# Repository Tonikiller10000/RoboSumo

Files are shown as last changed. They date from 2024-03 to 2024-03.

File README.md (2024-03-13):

# RoboSumo

## Description:

This is a SUMO robot for comperitions. It pushes the opponent\`s robot out of the ring.
    
It uses:
- ATmega328p-AU as an microcontroller(used in arduino uno);
- 16 or 20Mhz crystal resonator;
- [TB6612FNG](https://github.com/Tonikiller10000/MotorDriver_1) DC motor driver;
- [VL53L0x](https://github.com/Tonikiller10000/VL53L0x_DistanceSensor) distance sensor;
- LI-PO battery (7.2V)
- 2x DC motors with low torque high speed gear box
- robot suport (Wood, 3d printed or any low weight matherial)

<table>
  <tr>
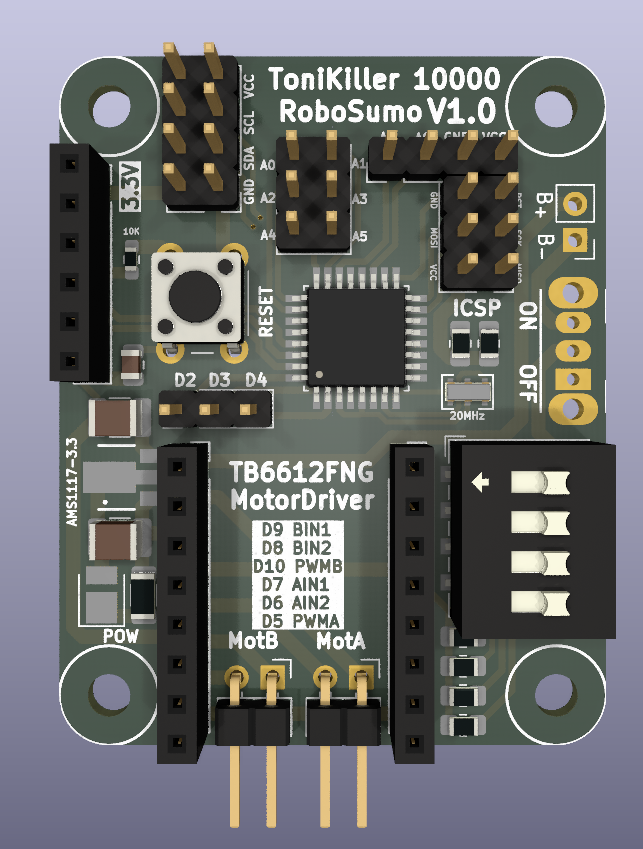
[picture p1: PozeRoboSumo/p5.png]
    <td></td>
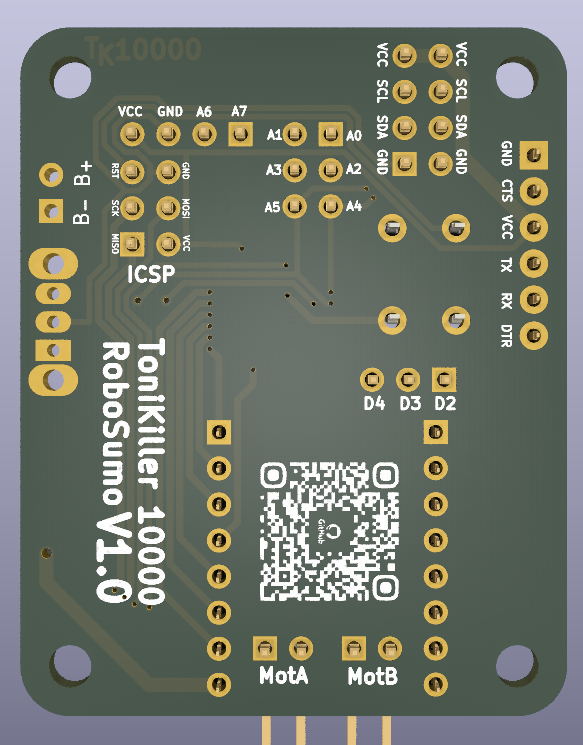
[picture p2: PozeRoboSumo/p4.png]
    <td></td>
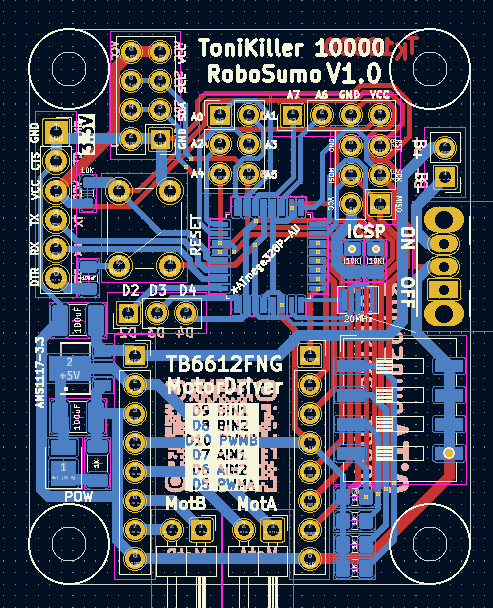
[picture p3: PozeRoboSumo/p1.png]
    <td></td>
  </tr>
</table>

Schematic:
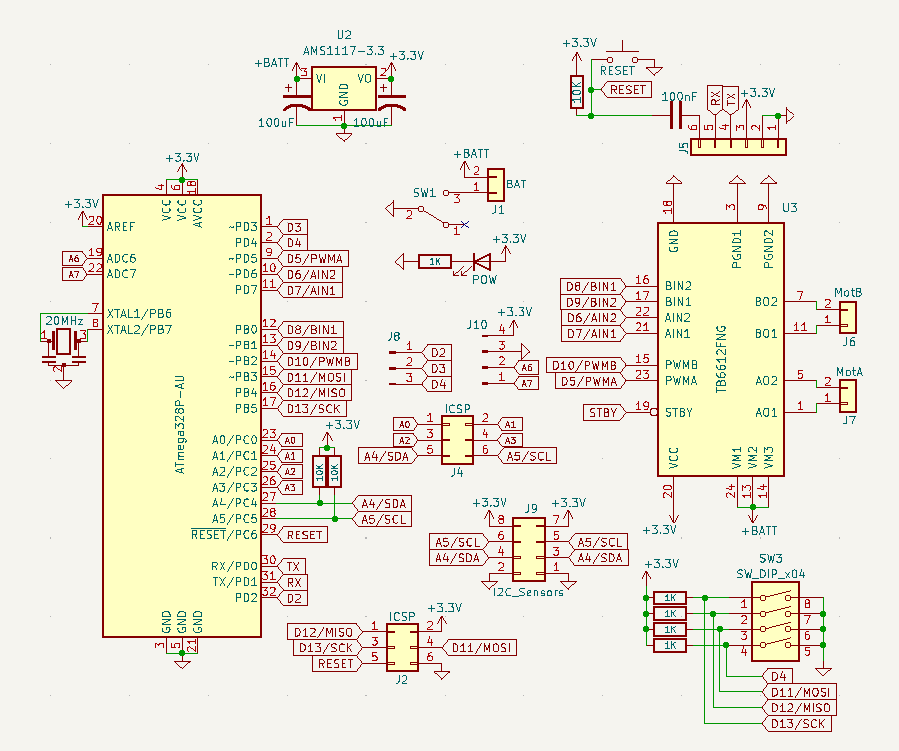
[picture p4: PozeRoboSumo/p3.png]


### How it works:
The board is like a custom arduino UNO board powered from an 7.2V Li-Po battery trouth an 5V voltage regulator. 6 digital pins are used for the TB6612FNG motor driver witch is powered dirrectly from the battery to give more power to the motors. The reset pin has a 10K pullup resistor witch is pulled down by the reset button when it is pressed. The UART and ICSP pins wore pulled out to program the code and the bootloader of the IC.
For now I will try to use the [VL53L0x](https://github.com/Tonikiller10000/VL53L0x_DistanceSensor) I2C distance sensor, because [other sensors](https://github.com/Tonikiller10000/RoboSumo/blob/main/PozeRoboSumo/s1.png) are a little to slow.

### Programming:
Programming of the robot is done via UART protocoll with an [FTDI](https://github.com/Tonikiller10000/CH340G-FTDI-PROGRAMER) programming board. The code for the RoboSumo is not ready. 
 
### Design and mentions

This is The model I followed and some tips:
- to reach better torque on the wheels, it should be wider. 
- to mount the motors use molderd plastic motor holders, or be carefull when printing [it](https://github.com/Tonikiller10000/LineFollower/blob/main/LineFollower_Pictures/w1.jpg). 
- the case was made with autodesk fusion 360 at the 3d printer and with some M3 screws.

<table>
  <tr>
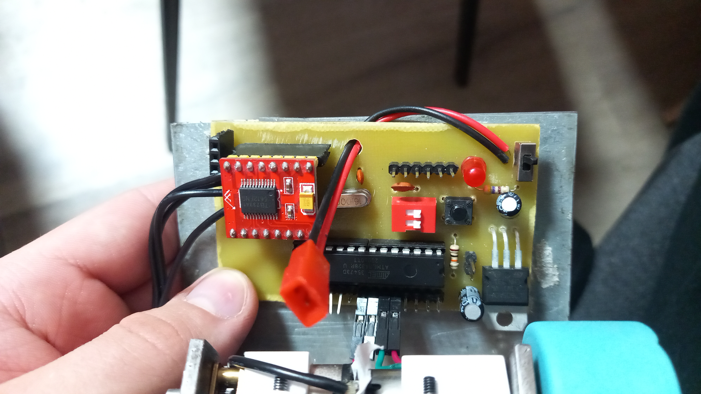
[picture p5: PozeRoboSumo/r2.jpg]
    <td></td>
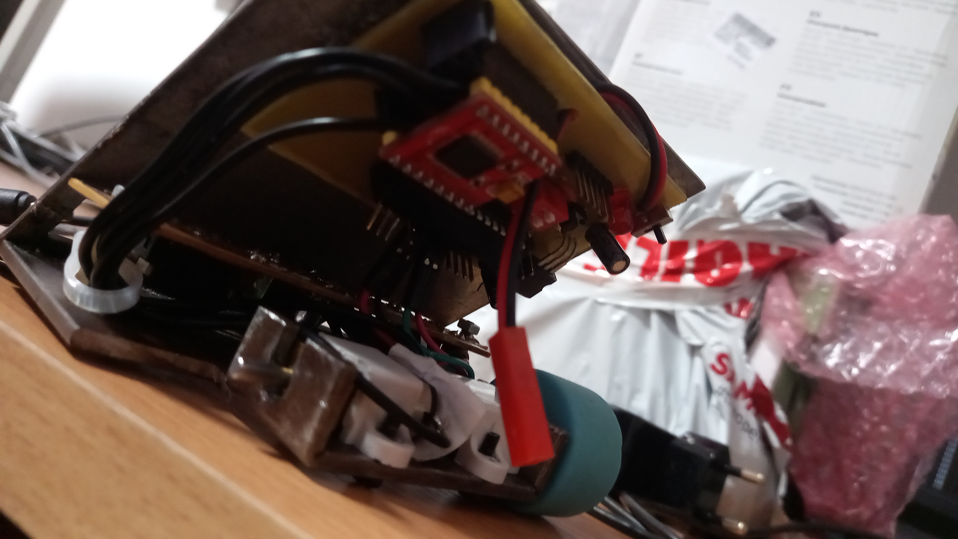
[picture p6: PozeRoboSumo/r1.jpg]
    <td></td>
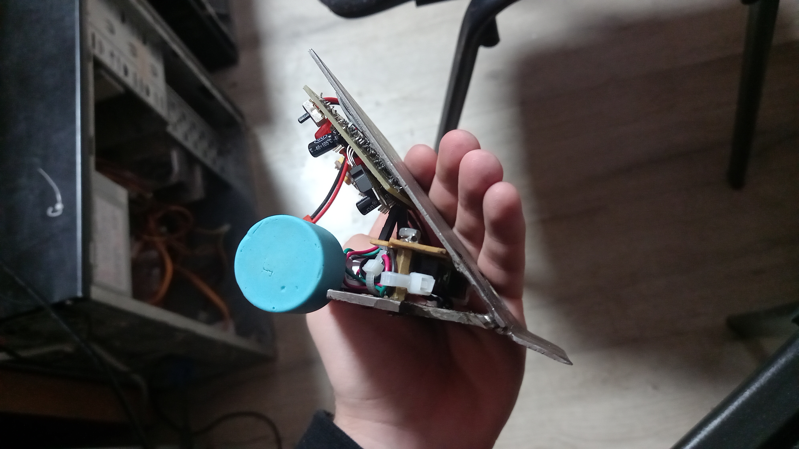
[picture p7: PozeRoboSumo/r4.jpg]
    <td></td>
  </tr>
</table>

The next version will have the motor driver soldered on the board and motors screwed dirrectly to it as the suport. Also I will try to make a smaller version

## Links: 
- ATmega328p-AU (microcontroller): 
- LM78L05 (5V voltage regulator):

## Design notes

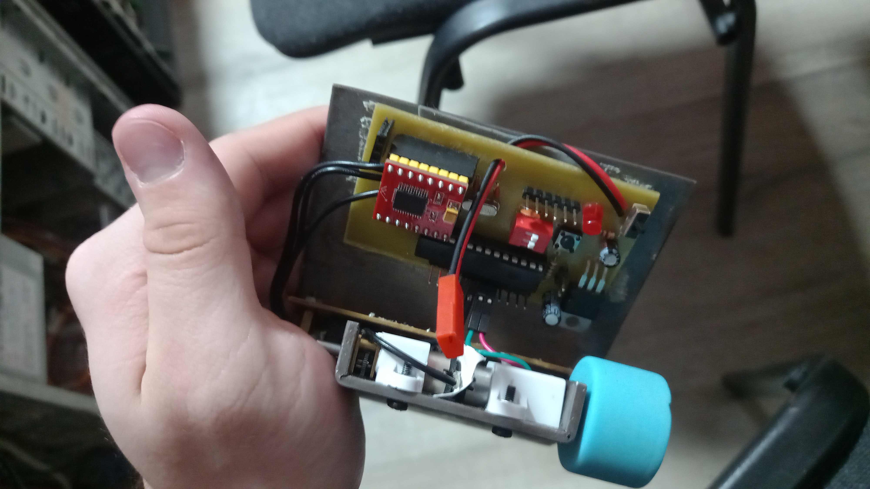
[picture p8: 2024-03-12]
PozeRoboSumo/r5.jpg

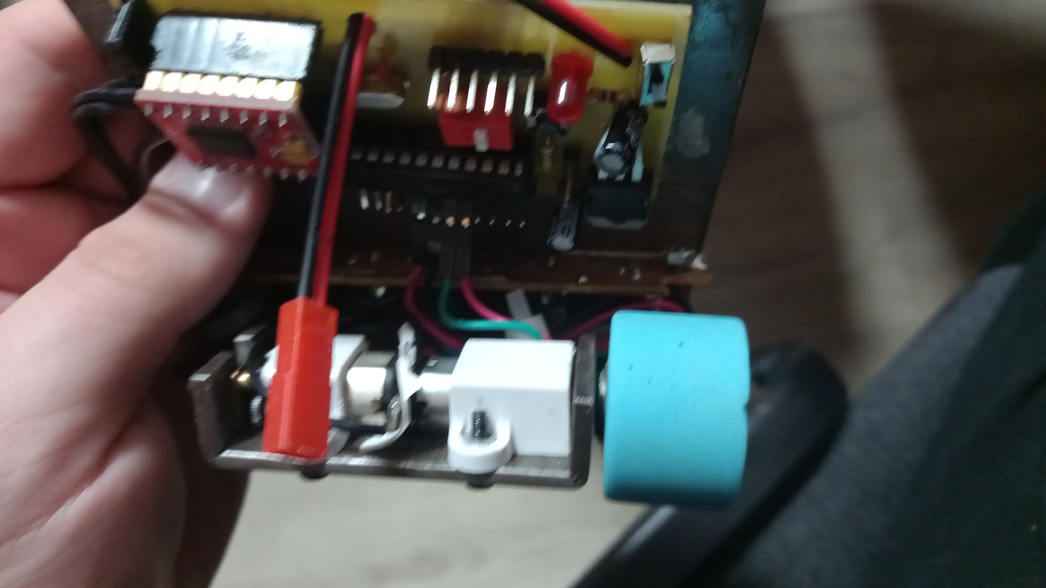
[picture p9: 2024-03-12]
PozeRoboSumo/r3.jpg

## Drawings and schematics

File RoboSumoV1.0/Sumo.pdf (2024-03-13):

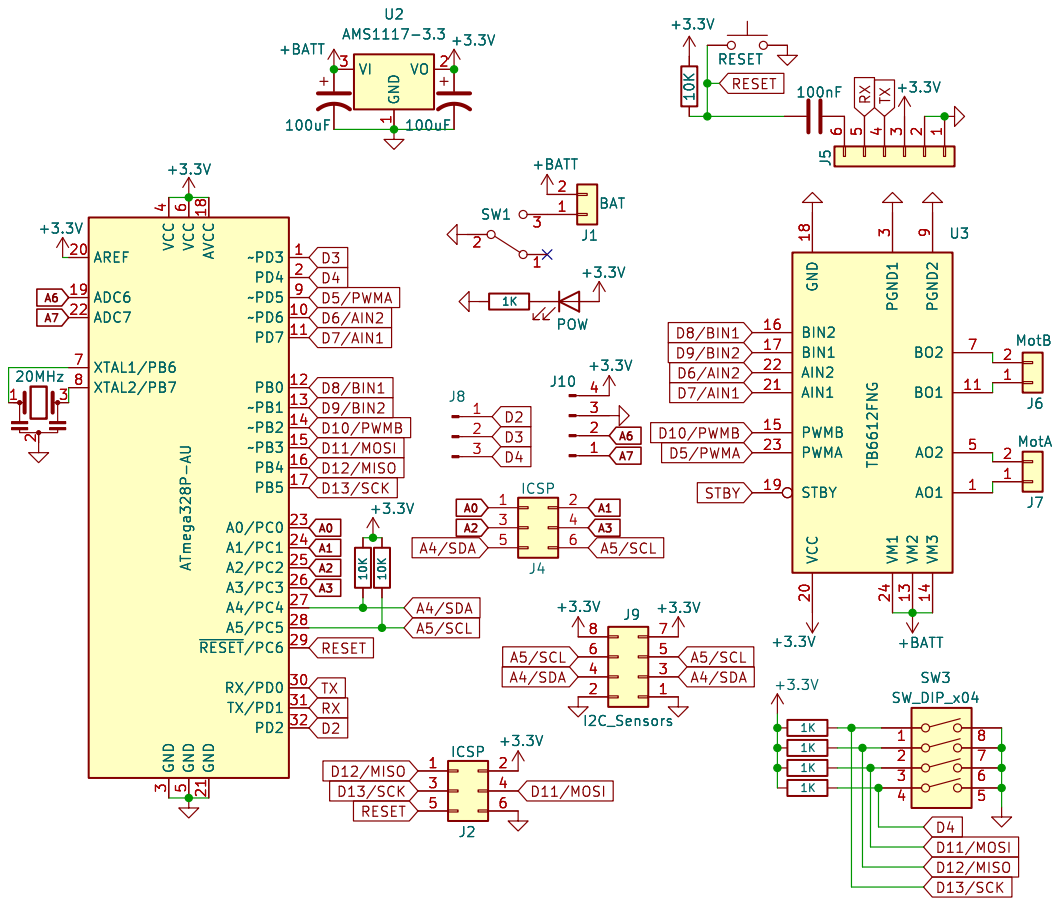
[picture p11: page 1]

Id: 1/1 Title: File: Sumo.kicad_sch Sheet: / 123

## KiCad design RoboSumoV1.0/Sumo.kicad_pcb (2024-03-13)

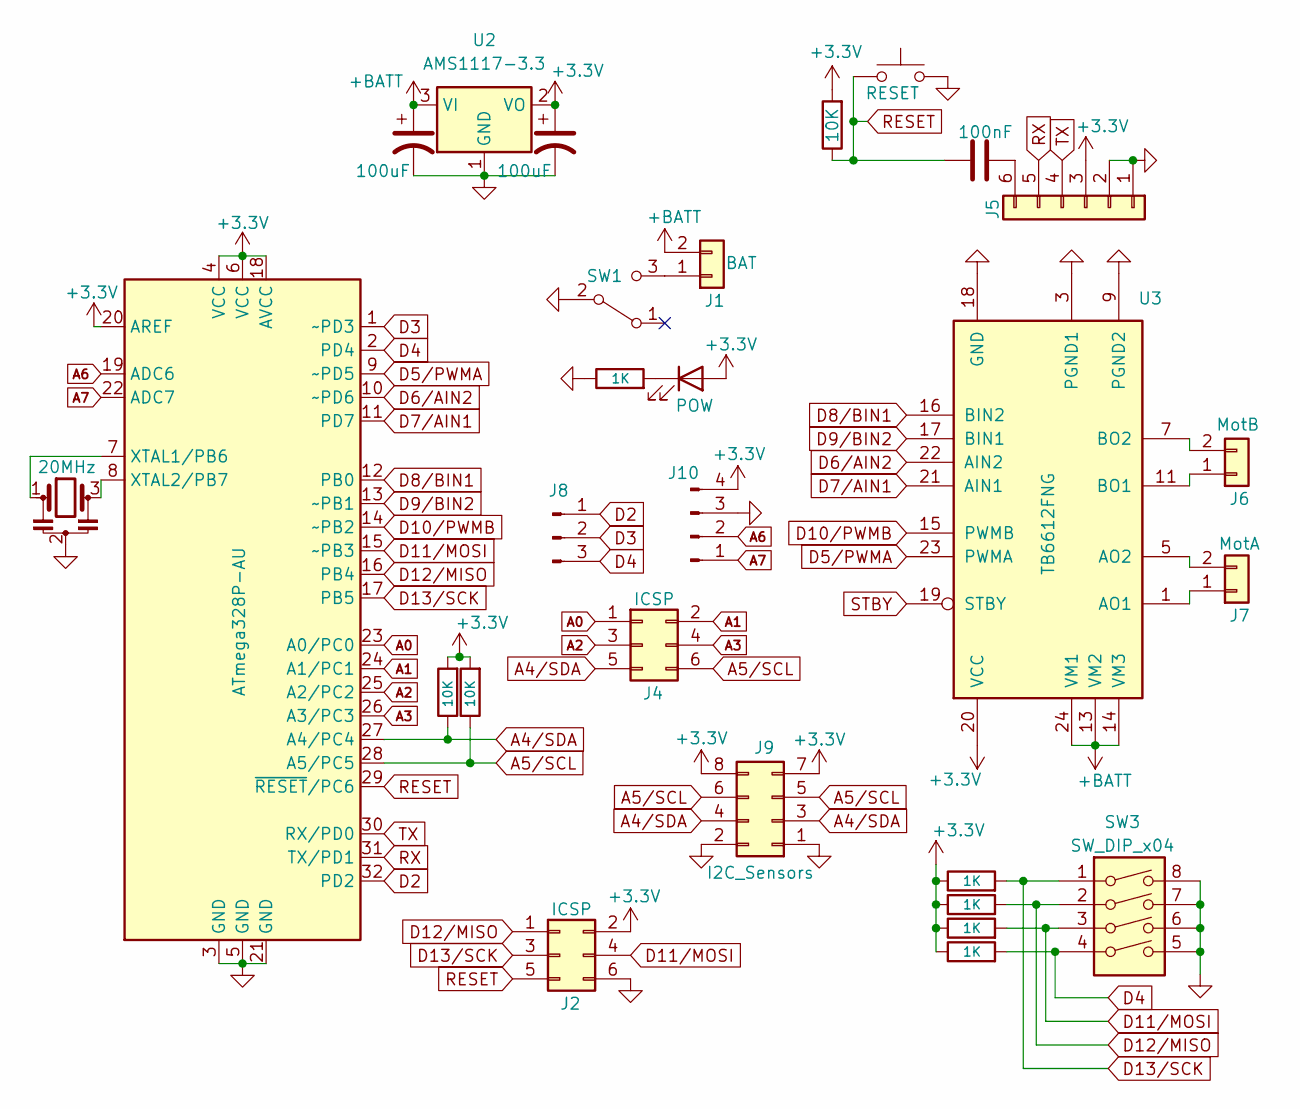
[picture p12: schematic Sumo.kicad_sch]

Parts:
C1, C2: 100uF; C_1210_3225Metric_Pad1.33x2.70mm_HandSolder
C3: 100nF; C_0805_2012Metric
D1: POW
J1: BAT; PinHeader_1x02_P2.54mm_Vertical
J2, J4: ICSP; PinHeader_2x03_P2.54mm_Vertical
J5: Conn_01x06_MountingPin
J6: MotB; PinHeader_1x02_P2.54mm_Horizontal
J7: MotA; PinHeader_1x02_P2.54mm_Horizontal
J8: Conn_01x03_Pin
J9: I2C_Sensors
J10: Conn_01x04_Pin
R1, R7, R8, R9, R10: 1K; R_1206_3216Metric
R2, R11, R12: 10K; R_1206_3216Metric
SW1: SW_SPDT
SW2: RESET
SW3: SW_DIP_x04
U1: ATmega328P-AU; TQFP-32_7x7mm_P0.8mm
U2: AMS1117-3.3; SOT-223-3_TabPin2
U3: TB6612FNG; SSOP-24_5.3x8.2mm_P0.65mm
Y1: 20MHz; Resonator_SMD_Murata_CSTxExxV-3Pin_3.0x1.1mm

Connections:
+5V: C2.1, D1.2 (A), J2.2, J5.3, J9.7, J9.8, J10.4, R2.2, R7.1, R8.1, R9.1, R10.1, R11.2, R12.2, U1.4 (VCC), U1.6 (VCC), U1.18 (AVCC), U1.20 (AREF), U2.2 (VO); also elsewhere on the board
+BATT: C1.1, J1.2, U2.3 (VI); also elsewhere on the board
A0: J4.1, U1.23 (A0/PC0)
A1: J4.2, U1.24 (A1/PC1)
A2: J4.3, U1.25 (A2/PC2)
A3: J4.4, U1.26 (A3/PC3)
A4/SDA: J4.5, J9.3, J9.4, R11.1, U1.27 (A4/PC4)
A5/SCL: J4.6, J9.5, J9.6, R12.1, U1.28 (A5/PC5)
A6: J10.2, U1.19 (ADC6)
A7: J10.1, U1.22 (ADC7)
D2: J8.1, U1.32 (PD2)
D3: J8.2, U1.1 (~PD3)
D4: J8.3, R10.2, SW3.4, U1.2 (PD4)
D5/PWMA: U1.9 (~PD5), U3.23 (PWMA); also elsewhere on the board
D6/AIN2: U1.10 (~PD6), U3.22 (AIN2); also elsewhere on the board
D7/AIN1: U1.11 (PD7), U3.21 (AIN1); also elsewhere on the board
D8/BIN1: U1.12 (PB0), U3.16 (BIN2); also elsewhere on the board
D9/BIN2: U1.13 (~PB1), U3.17 (BIN1); also elsewhere on the board
D10/PWMB: U1.14 (~PB2), U3.15 (PWMB); also elsewhere on the board
D11/MOSI: J2.4, R9.2, SW3.3, U1.15 (~PB3)
D12/MISO: J2.1, R8.2, SW3.2, U1.16 (PB4)
D13/SCK: J2.3, R7.2, SW3.1, U1.17 (PB5)
GND: C1.2, C2.2, J2.6, J5.1, J5.2, J9.1, J9.2, J10.3, R1.1, SW1.2 (B), SW2.1, SW3.5, SW3.6, SW3.7, SW3.8, U1.3 (GND), U1.5 (GND), U1.21 (GND), U2.1 (GND), Y1.2; also elsewhere on the board
unnamed: D1.1 (K), R1.2
unnamed: J1.1, SW1.3 (C)
unnamed: C3.1, J5.6
unnamed 26: J6.1; also elsewhere on the board
unnamed 27: J6.2; also elsewhere on the board
unnamed 28: J7.1; also elsewhere on the board
unnamed 29: J7.2; also elsewhere on the board
unnamed: U1.7 (XTAL1/PB6), Y1.1
unnamed: U1.8 (XTAL2/PB7), Y1.3
RESET: C3.2, J2.5, R2.1, SW2.2, U1.29 (~RESET/PC6)
RX: J5.5, U1.31 (TX/PD1)
TX: J5.4, U1.30 (RX/PD0)

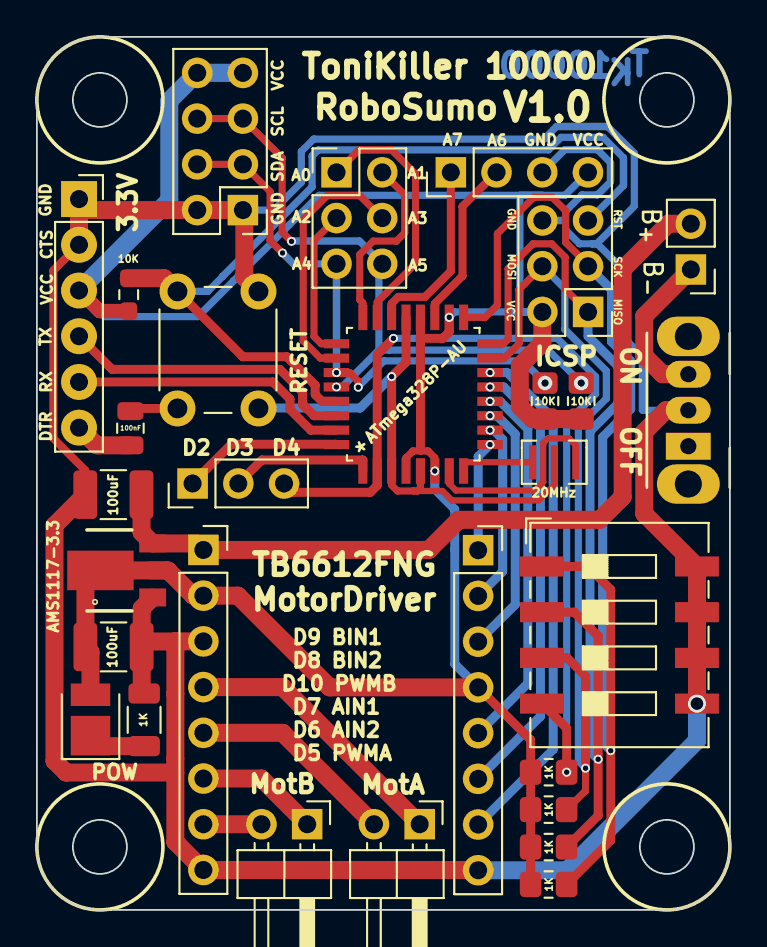
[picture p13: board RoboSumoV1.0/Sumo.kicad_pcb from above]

Board: 2 copper layers, 38.5 x 48.5 mm, 29 parts (0 on the bottom side), 35 nets.

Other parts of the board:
J20: BAT; PinSocket_1x08_P2.54mm_Vertical
J21: Conn_01x03; PinSocket_1x08_P2.54mm_Vertical

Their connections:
+5V: J20.2, J21.4; also elsewhere on the board
+BATT: J20.1; also elsewhere on the board
D5/PWMA: J21.1; also elsewhere on the board
D6/AIN2: J21.2; also elsewhere on the board
D7/AIN1: J21.3; also elsewhere on the board
D8/BIN1: J21.5; also elsewhere on the board
D9/BIN2: J21.6; also elsewhere on the board
D10/PWMB: J21.7; also elsewhere on the board
GND: J20.3, J20.8, J21.8; also elsewhere on the board
unnamed 26: J20.6; also elsewhere on the board
unnamed 27: J20.7; also elsewhere on the board
unnamed 28: J20.4; also elsewhere on the board
unnamed 29: J20.5; also elsewhere on the board

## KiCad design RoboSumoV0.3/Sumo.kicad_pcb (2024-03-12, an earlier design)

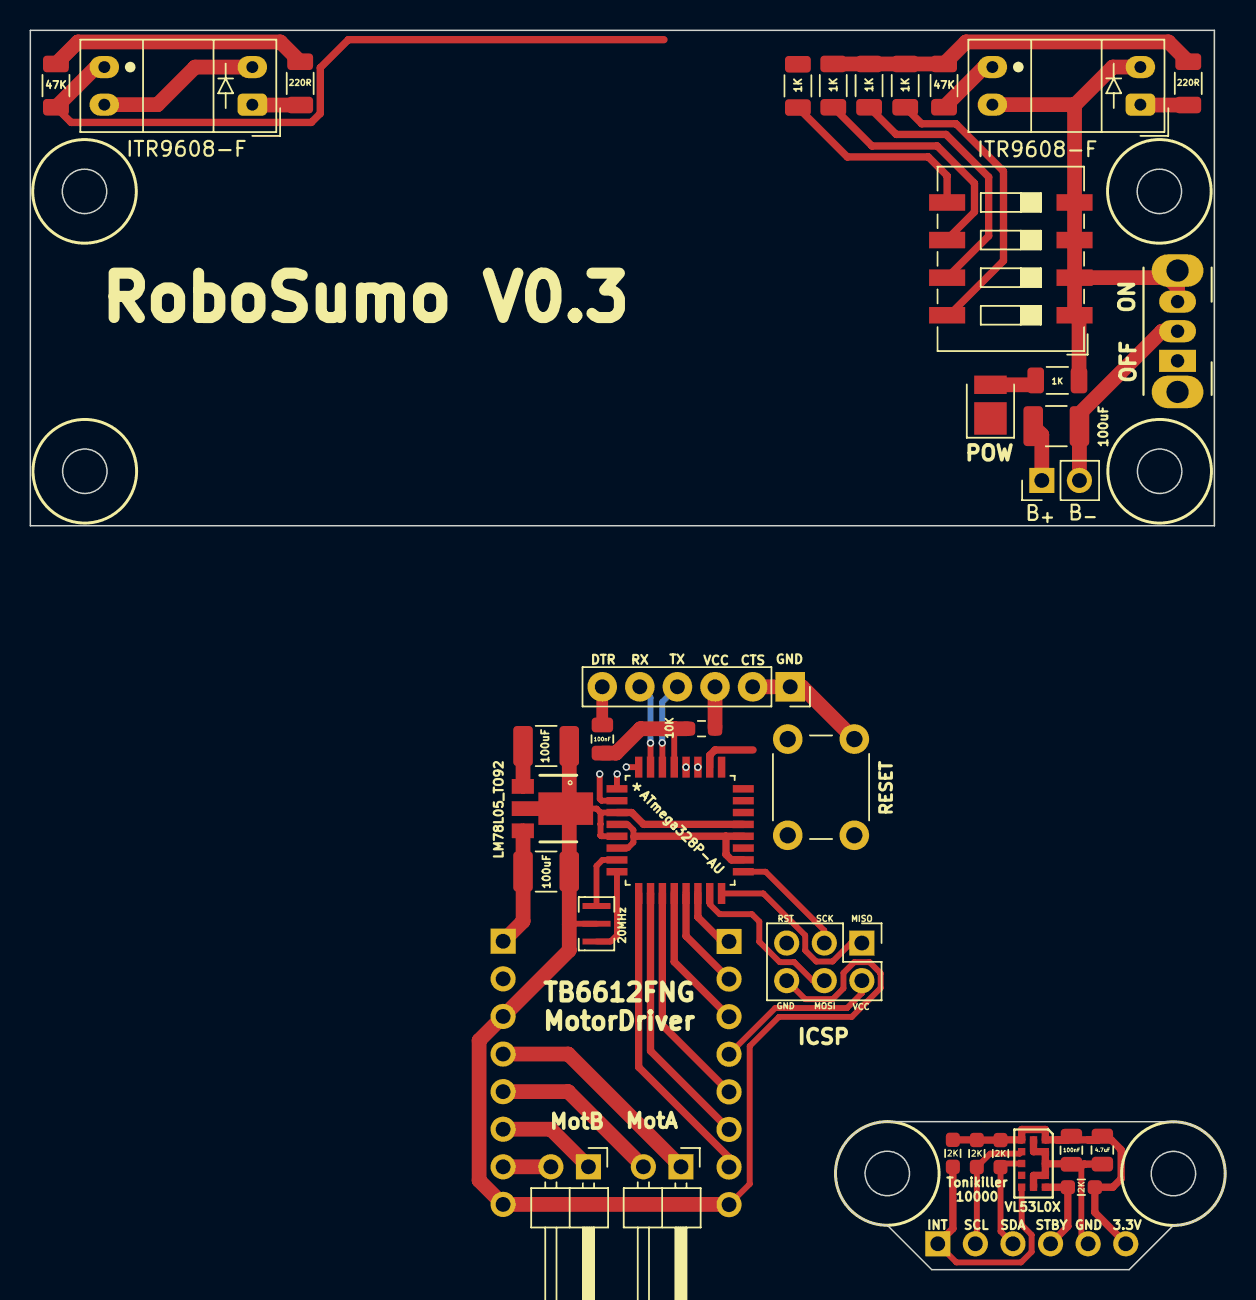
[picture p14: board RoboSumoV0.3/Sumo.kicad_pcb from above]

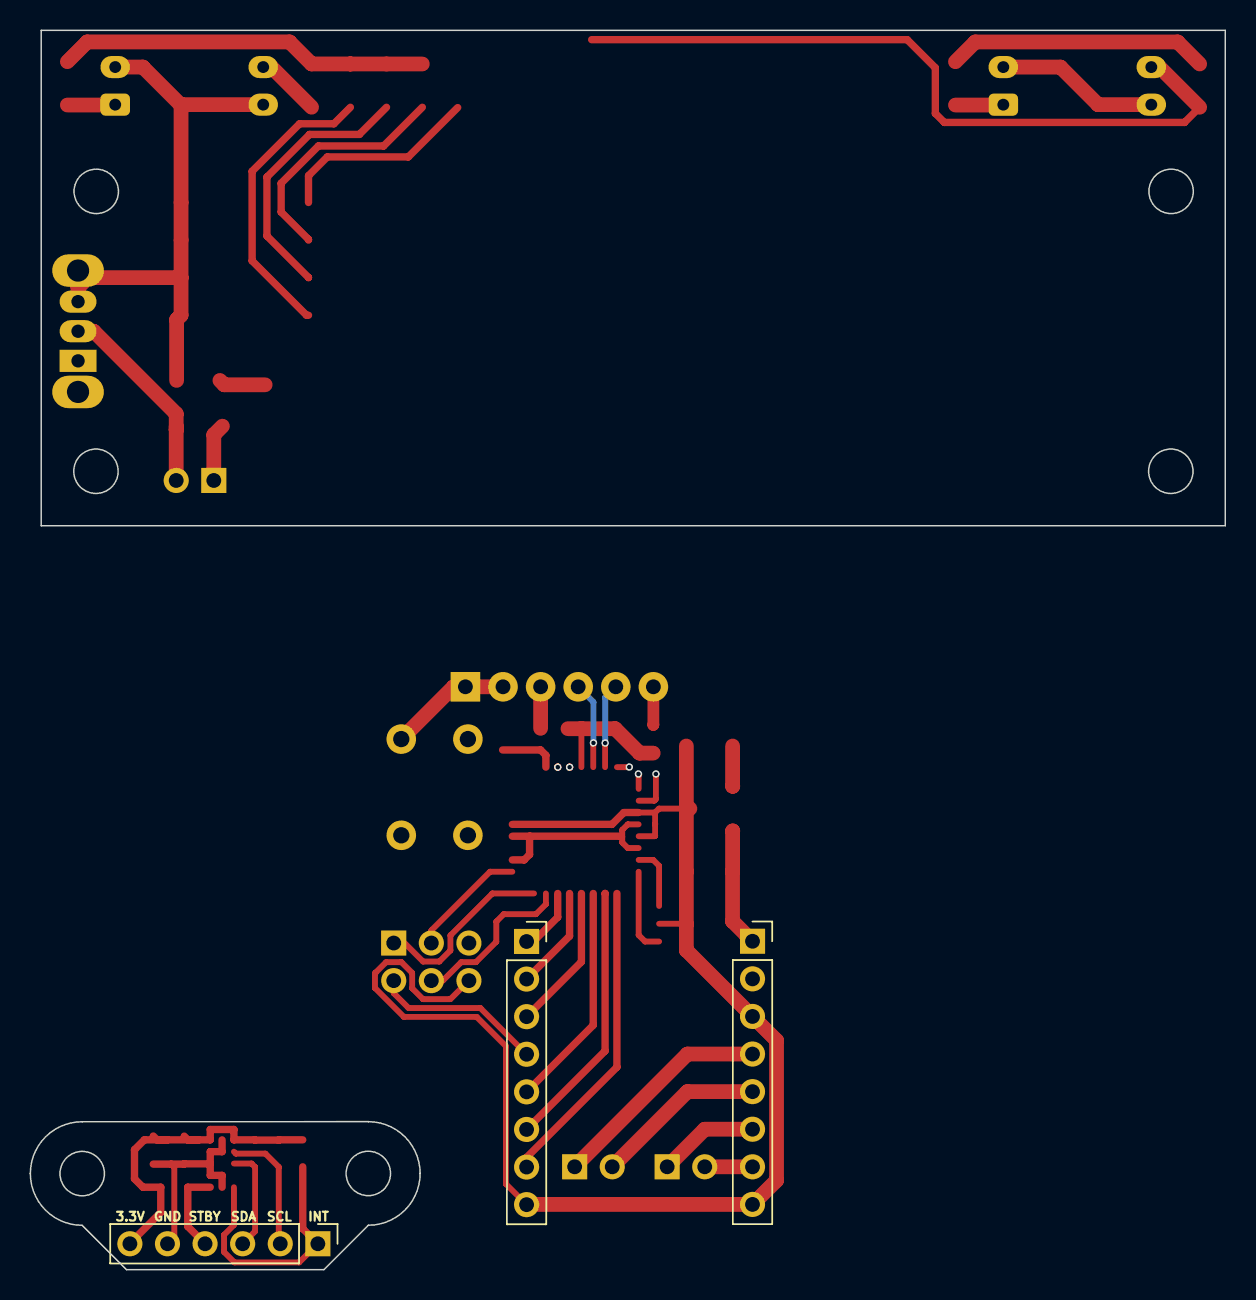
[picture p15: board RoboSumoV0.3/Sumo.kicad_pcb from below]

Board: 2 copper layers, 80.7 x 83.7 mm, 35 parts (2 on the bottom side), 27 nets.

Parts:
C1, C1#2, C2: 100uF; C_1210_3225Metric_Pad1.33x2.70mm_HandSolder
C3, C3#2: 100nF; C_0805_2012Metric
C3#3: 4.7uF; C_0805_2012Metric
D1: POW; LED_PLCC_2835
J1: BAT; PinHeader_1x02_P2.54mm_Vertical
J2: ICSP; PinHeader_2x03_P2.54mm_Vertical
J4: Conn_01x06_MountingPin; PinSocket_1x06_P2.54mm_Vertical
J6: MotB; PinHeader_1x02_P2.54mm_Horizontal
J7: MotA; PinHeader_1x02_P2.54mm_Horizontal
J8: BAT; PinSocket_1x08_P2.54mm_Vertical
J9: Conn_01x03; PinSocket_1x08_P2.54mm_Vertical
R1: 10K; R_0603_1608Metric_Pad0.98x0.95mm_HandSolder
R1#2, R1#3, R1#4, R1#5: 2K; R_0603_1608Metric_Pad0.98x0.95mm_HandSolder
R2, R20, R20#2, R20#3, R20#4: 1K; R_1206_3216Metric
R3, R5: 220R; R_1206_3216Metric
R4, R6: 47K; R_1206_3216Metric
SW1: RESET; SW_CuK_OS102011MA1QN1_SPDT_Angled
SW2: RESET; SW_PUSH_6mm
U1: ATmega328P-AU; TQFP32_32A_MCH
U2: LM78L05_TO92; PK(R-PSSO-F3)
U4, U5: ITR9608-F; Everlight_ITR9608-F
Y1: 20MHz; Resonator_SMD_Murata_CSTxExxV-3Pin_3.0x1.1mm

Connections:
0V: C1#2.2, C2.2, D1.1 (K), J2.6, J4.1, J4.2, J8.3, J8.8, J9.8, R2.2, SW1.3, SW2.2, U1.3 (GND), U1.5 (GND), U1.21 (GND), U2.2 (GND), U4.2, U4.4, U5.2, U5.4, Y1.2
5V: C2.1, J2.2, J4.3, J9.4, R3.2, R4.1, R5.2, R6.1, R20.1, R20#2.1, R20#3.1, R20#4.1, U1.4 (VCC), U1.6 (VCC), U1.18 (AVCC), U1.20 (AREF), U2.1 (VO)
+BATT: C1.1, C1#2.1, J1.1, J8.1, U2.3 (VI)
AIN1: J9.3, U1.12 (PB0), U1.32 (PD2)
AIN2: J9.2, U1.2 (PD4), U1.13 (~PB1)
BIN1: J9.5, U1.11 (PD7)
BIN2: J9.6, U1.10 (~PD6)
MISO: J2.1, U1.16 (PB4)
MOSI: J2.4, U1.15 (~PB3)
unnamed: D1.2 (A), R2.1
unnamed: C1.2, J1.2, SW1.2
unnamed: J6.1, J8.6
unnamed: J6.x (Pin_2), J8.7
unnamed: J7.1, J8.4
unnamed: J7.2, J8.5
unnamed: R3.1, U4.1
unnamed: R5.1, U5.1
unnamed: U1.7 (XTAL1/PB6), Y1.1
unnamed: U1.8 (XTAL2/PB7), Y1.3
PWMA: J9.1, U1.1 (~PD3), U1.14 (~PB2)
PWMB: J9.7, U1.9 (~PD5)
RESET: C3.2, J2.5, R1.1, SW2.1, U1.29 (~RESET/PC6)
RX: J4.5, U1.31 (TX/PD1)
SCK: J2.3, U1.17 (PB5)
Sensor4: R6.2, U1.27 (A4/PC4), U5.3
Sensor5: R4.2, U1.28 (A5/PC5), U4.3
TX: J4.4, U1.30 (RX/PD0)

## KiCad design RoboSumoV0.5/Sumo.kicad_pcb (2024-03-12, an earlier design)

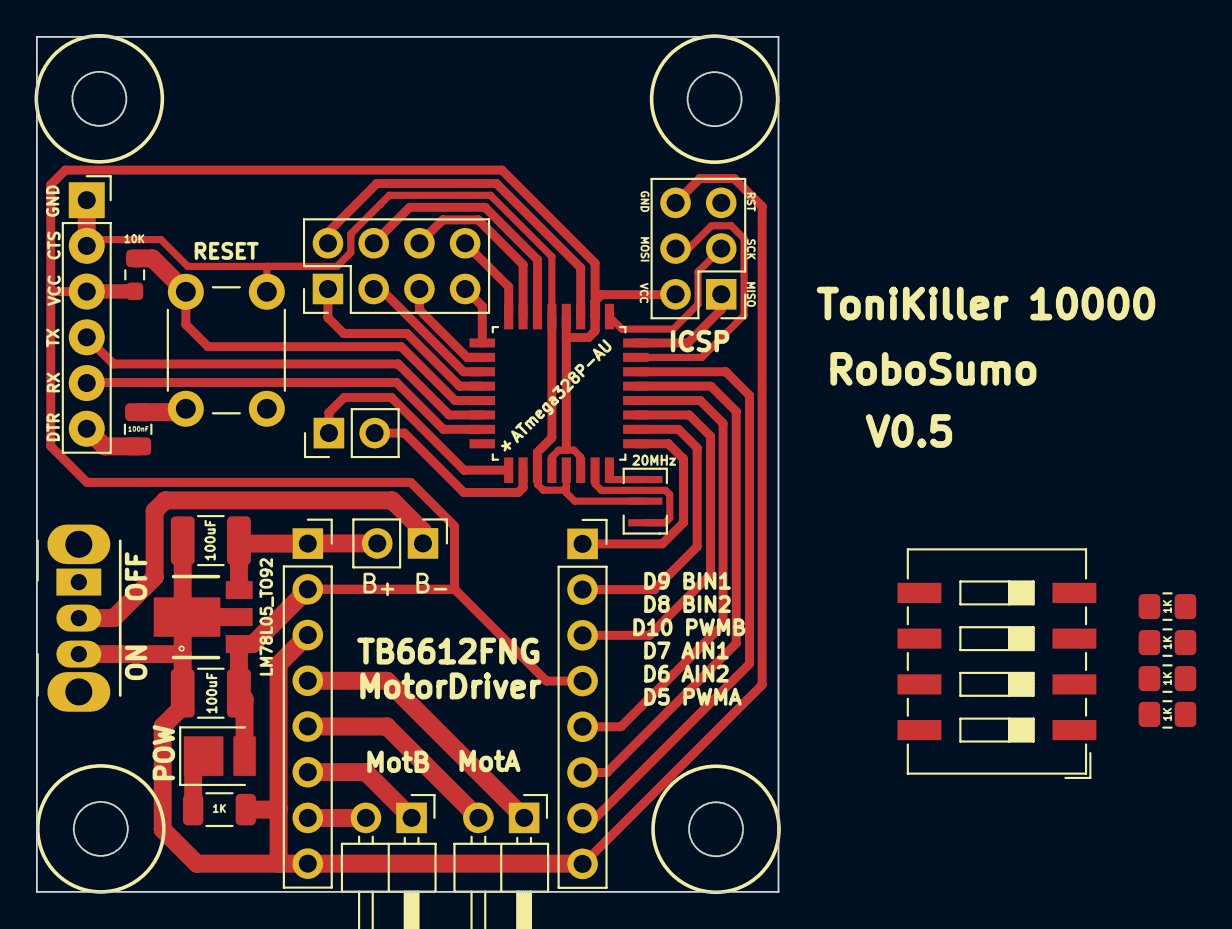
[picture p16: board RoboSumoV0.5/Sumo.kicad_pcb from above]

Board: 2 copper layers, 41.2 x 47.5 mm, 24 parts (0 on the bottom side), 27 nets.

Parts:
C1, C2: 100uF; C_1210_3225Metric_Pad1.33x2.70mm_HandSolder
C3: 100nF; C_0805_2012Metric
D1: POW; LED_PLCC_2835
J1, J1#2: BAT; PinHeader_1x02_P2.54mm_Vertical
J2: ICSP; PinHeader_2x03_P2.54mm_Vertical
J5: Conn_01x06_MountingPin; PinSocket_1x06_P2.54mm_Vertical
J6: MotB; PinHeader_1x02_P2.54mm_Horizontal
J7: MotA; PinHeader_1x02_P2.54mm_Horizontal
J8: BAT; PinSocket_1x08_P2.54mm_Vertical
J9: Conn_01x03; PinSocket_1x08_P2.54mm_Vertical
R1: 1K; R_1206_3216Metric
R2: 10K; R_0603_1608Metric_Pad0.98x0.95mm_HandSolder
R7, R8, R9, R10: 1K; R_0805_2012Metric_Pad1.20x1.40mm_HandSolder
SW1: SW_SPDT; SW_CuK_OS102011MA1QN1_SPDT_Angled
SW2: RESET; SW_PUSH_6mm
SW3: SW_DIP_x04; SW_DIP_SPSTx04_Slide_9.78x12.34mm_W8.61mm_P2.54mm
U1: ATmega328P-AU; TQFP32_32A_MCH
U2: LM78L05_TO92; PK(R-PSSO-F3)
Y1: 20MHz; Resonator_SMD_Murata_CSTxExxV-3Pin_3.0x1.1mm

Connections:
+5V: C2.1, D1.2 (A), J2.2, J5.3, J8.2, J9.4, R2.2, R7.1, R8.1, R9.1, R10.1, U1.4 (VCC), U1.6 (VCC), U1.18 (AVCC), U1.20 (AREF), U2.1 (VO)
+BATT: C1.1, J1#2.2, J8.1, U2.3 (VI)
AIN1: J9.3, U1.11 (PD7)
AIN2: J9.2, U1.10 (~PD6)
BIN1: J9.5, U1.12 (PB0)
BIN2: J9.6, U1.13 (~PB1)
DTR: C3.1, J5.6
GND: C1.2, C2.2, J2.6, J5.1, J5.2, J8.3, J8.8, J9.8, R1.1, SW1.3 (C), SW2.1, SW3.5, SW3.6, SW3.7, SW3.8, U1.3 (GND), U1.5 (GND), U1.21 (GND), U2.2 (GND), Y1.2
MISO: J2.1, U1.16 (PB4)
MOSI: J2.4, U1.15 (~PB3)
unnamed: D1.1 (K), R1.2
unnamed: J1#2.1, SW1.2 (B)
unnamed: J6.1, J8.6
unnamed: J7.1, J8.4
unnamed: J7.2, J8.5
unnamed: R7.2, SW3.1
unnamed: R8.2, SW3.2
unnamed: R9.2, SW3.3
unnamed: R10.2, SW3.4
unnamed: U1.7 (XTAL1/PB6), Y1.1
unnamed: U1.8 (XTAL2/PB7), Y1.3
PWMA: J9.1, U1.9 (~PD5)
PWMB: J9.7, U1.14 (~PB2)
RESET: C3.2, J2.5, R2.1, SW2.2, U1.29 (~RESET/PC6)
RX: J5.5, U1.31 (TX/PD1)
SCK: J2.3, U1.17 (PB5)
TX: J5.4, U1.30 (RX/PD0)

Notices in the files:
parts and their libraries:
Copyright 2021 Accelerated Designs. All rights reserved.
